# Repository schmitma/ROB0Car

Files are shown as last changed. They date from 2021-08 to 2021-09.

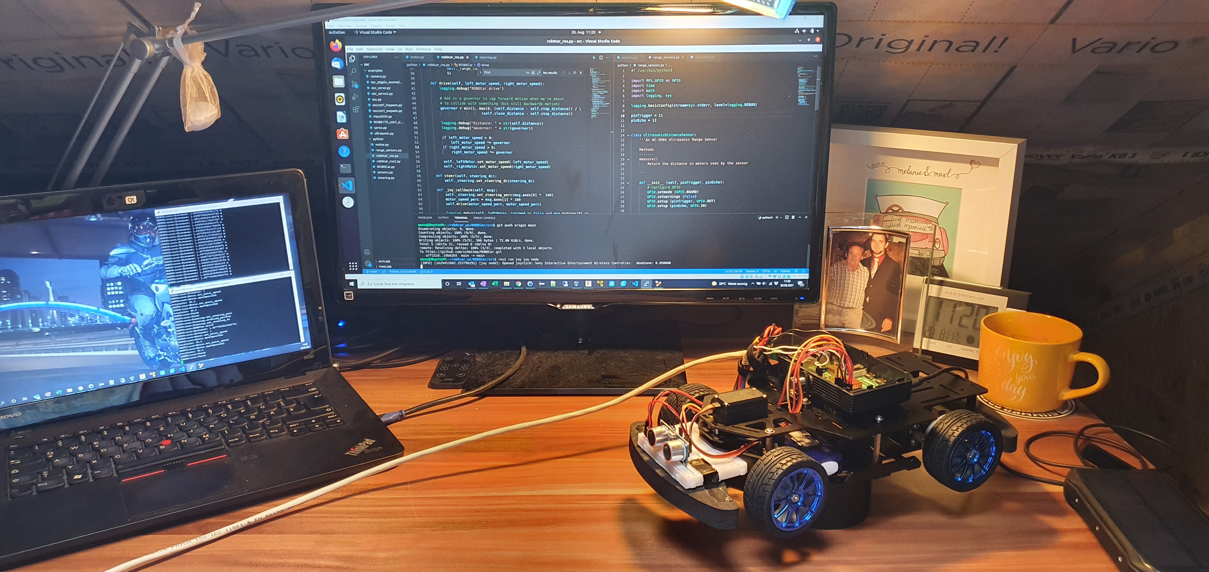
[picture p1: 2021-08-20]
doc/img/20210820_112039.jpg

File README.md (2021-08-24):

# ROB0Car
Build and control an AI-enabled autonomous robot car using the Raspberry Pi, ROS, Python and C/C++

Core-technologies to be used:
 - Raspberry Pi
 - Ubuntu
 - ROS2
 - Python
 - C/C++
 - Visual Studio Code as Editor/IDE
 - SCM using git
 - CAD using Fusion 360
 - 3D-printing using Creality Ender 3 Pro
 - Using AI methods such as neuronal networks

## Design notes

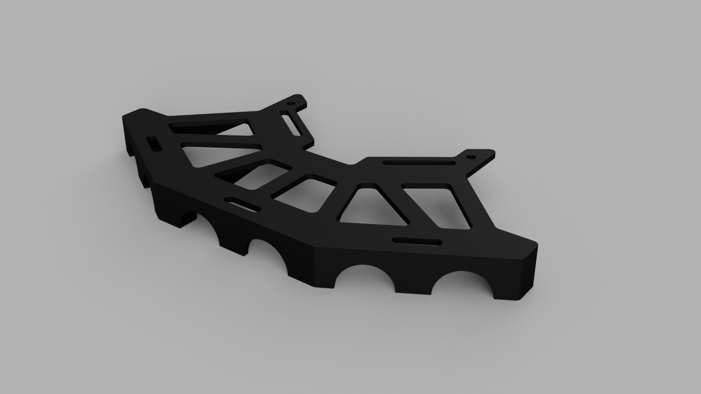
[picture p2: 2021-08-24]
cad/renderings/Front_Mount_HC-SR04.png

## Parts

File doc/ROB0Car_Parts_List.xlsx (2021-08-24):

Picture | Manufacturer | Description | Manufacturer Article Number | EAN | Status | (Estimated) Delivery Date | Stock | Source of supply | Comment | Unit Price incl. VAT [€] | Quantity | Unit | Total Price incl. VAT [€]
 | LABISTS | LABISTS Raspberry Pi 4 Model B 4 GB Ultimatives Kit mit 32GB Class10 Micro SD-Karte, 5,1V 3,0A USB-C EIN/Aus-Schaltnetzteil, 3 Premium Kupfer Kühlkörper, Micro HDMI-Kabel, Premium Schwarzes Gehäuse | B09B9M7TPP |  | In Stock |  | 1.00 | https://www.amazon.de/Raspberry-Ultimatives-Aus-Schaltnetzteil-HDMI-Kabel-K%C3%BChlk%C3%B6rper/dp/B09B9M7TPP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 |  | 87.99 € | 1.00 | pc | 87.99 €
 | WayinTop | WayinTop Ultimate Starter Kit für Raspberry Pi 4 B 3 B+, Ausführliche E-Book Anleitung, Python C Java, 300 Elemente, Elektronische Kit für Raspberry Pi zum Lernen Elektronik und Programmierung |  |  | In Stock |  | 1.00 | https://www.amazon.de/gp/product/B08DQYLLNZ/ref=ppx_yo_dt_b_asin_title_o01_s00?ie=UTF8&psc=1 |  | 34.19 € | 1.00 | pc | 34.19 €
 | LABISTS | LABISTS Ultimate Starter Kit, Raspberry Pi Starter Kit, Support Python C, mit kostenlosen Tutorials, Lötfreies Steckbrett und Zubehör |  |  | In Stock |  | 1.00 |  |  | 44.79 € | 1.00 | pc | 44.79 €
 | DFRobot | DFRobot ROB0170 NXP CUP Race Car Chassis | ROB0170 |  | In Stock |  | 1.00 | https://www.mouser.de/ProductDetail/DFRobot/ROB0170?qs=hWgE7mdIu5TqrtXq%252BmF5EA%3D%3D |  | 86.98 € | 1.00 | pc | 86.98 €
 | DFRobot | DFRobot KIT0166 Brushless DC Motor-Kit for ROB0170 | KIT0166 |  | In Stock |  | 1.00 | https://www.mouser.de/ProductDetail/DFRobot/KIT0166 |  | 38.55 € | 1.00 | pc | 38.55 €
 |  | HC-SR04 Ultraschall-Modul Entfernungssensor für Raspberry Pi, UNO, MEGA2560, Roboter (blau), 5 Stück |  |  | In Stock |  | 2.00 | https://www.amazon.de/gp/product/B081PZF4T3/ref=ppx_yo_dt_b_asin_title_o01_s00?ie=UTF8&psc=1 |  | 7.99 € | 2.00 | pc | 15.98 €
 |  | Schutzmatten 60 x 60cm Schutzmatte Trainingsmatte Puzzlematte Unterlegmatten Poolmatte Fitnessmatten für Bodenschut für Bodenschutz, Büro, Fitnessraum, Bordures |  |  | In Stock |  | 1.00 | https://www.amazon.de/gp/product/B08SQ6NZXJ/ref=ppx_yo_dt_b_asin_title_o06_s00?ie=UTF8&psc=1 | Base for race track | 32.58 € | 1.00 | pc | 32.58 €
 | Arduino | ARDUINO UNO REV 3 |  |  | In Stock |  | 1.00 | https://www.amazon.de/gp/product/B008GRTSV6/ref=ppx_yo_dt_b_asin_title_o03_s00?ie=UTF8&psc=1 |  | 22.00 € | 1.00 | pc | 22.00 €
 | Youmile | Youmile 5 Stücke Geschwindigkeitsmesssensor IR Infrarot Schlitz Optokoppler Modul Lichtschranke Sensor für Motordrehzahlerkennung oder Arduino mit Encoder |  |  | In Stock |  | 1.00 | https://www.amazon.de/gp/product/B0817FM4BJ/ref=ppx_yo_dt_b_asin_title_o05_s01?ie=UTF8&psc=1 |  | 6.99 € | 1.00 | pc | 6.99 €
 | Youmile | Youmile 5 Stücke Geschwindigkeitsmesssensor LM393 Geschwindigkeitsmessmodul Tacho Sensor Slot Typ IR Optokoppler für MCU RPI Arduino DIY Kit mit Encoder |  |  | In Stock |  | 1.00 | https://www.amazon.de/gp/product/B0817H9436/ref=ppx_yo_dt_b_asin_title_o05_s00?ie=UTF8&psc=1 |  | 7.79 € | 1.00 | pc | 7.79 €
 | KINCREA | KINCREA 2.54mm Male Female Dupont Wire Jumper with Pin Header Connector Housing Kit - 620pcs JA001 |  |  | In Stock |  | 1.00 | https://www.amazon.de/gp/product/B07BTB3MC7/ref=ppx_yo_dt_b_asin_title_o02_s00?ie=UTF8&psc=1 |  | 12.99 € | 1.00 | pc | 12.99 €
 | Waveshare | Waveshare 2-DOF Pan-Tilt Hat for Raspberry Pi Zero/Zero W/Zero WH/2B/3B/3B+ Onboard PCA9685 PWM Chip TSL25911FN 16-bit Ambient Light Sensor Make Pi Camera Move and Sense Light Intensity Via I2C |  |  | In Stock |  | 1.00 | https://www.amazon.de/gp/product/B07PPV122Z/ref=ppx_yo_dt_b_asin_title_o01_s00?ie=UTF8&psc=1 |  | 24.99 € | 1.00 | pc | 24.99 €
 | Waveshare | Waveshare MCP23017 IO Expansion Board I2C Interface Expands 16 I/O Pins 8 pcs Stacked and Used at The Same Time Allow Multi I2C Modules to be Stacked |  |  | In Stock |  | 1.00 | https://www.amazon.de/gp/product/B07P2KD39X/ref=ppx_yo_dt_b_asin_title_o00_s00?ie=UTF8&psc=1 |  | 9.75 € | 1.00 | pc | 9.75 €
 | Turnigy | Turnigy E3 Compact 2S/3S Lipo Charger 100-240v (EU Plug) |  |  | In Stock |  | 1.00 | https://hobbyking.com/en_us/turnigy-e3-compact-2s-3s-lipo-charger-100-240v-eu-plug.html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 |  | 13.31 € | 1.00 | pc | 13.31 €
 | Turnigy | Turnigy nano-tech 1500mah 3S 35~70C Lipo Pack |  |  | In Stock |  | 1.00 | https://hobbyking.com/en_us/turnigy-nano-tech-1500mah-3s-35-70c-lipo-pack.html |  | 16.01 € | 1.00 | pc | 16.01 €
 |  | MT60 3 Pole Motor / ESC Connector Set 12AWG Black Male - Female (2 set) |  |  | In Stock |  | 2.00 | https://hobbyking.com/en_us/mt60-3-pole-motor-esc-connector-set-12awg-black-male-female-2-set.html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 |  | 3.05 € | 2.00 | pc | 6.10 €
 |  | Align Motor Pinion Gear 13T T-Rex 450 PRO # H45059 |  |  | In Stock |  | 2.00 | https://www.live-hobby.de/en/Accessories/Drives/Brushless-ESC-Motors/Motor-Pinion-Gear/Align-Motor-Pinion-Gear-13T-T-Rex-450-PRO-H45059.html |  | 3.79 € | 2.00 | pc | 7.58 €
 |  |  |  |  |  |  |  |  |  | Total Price incl. VAT [€] |  |  | 468.57 €

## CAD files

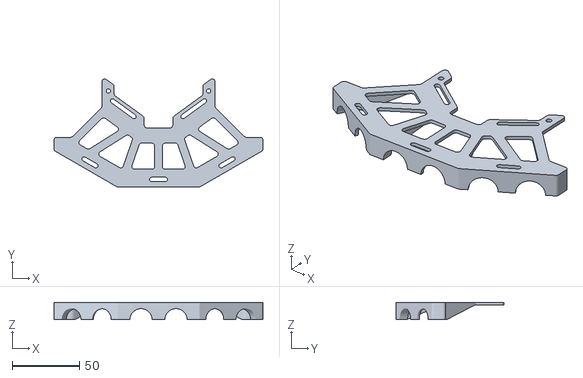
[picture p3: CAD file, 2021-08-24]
cad/Front_Mount_HC-SR04.stl
155.3 x 80.4 x 13.0

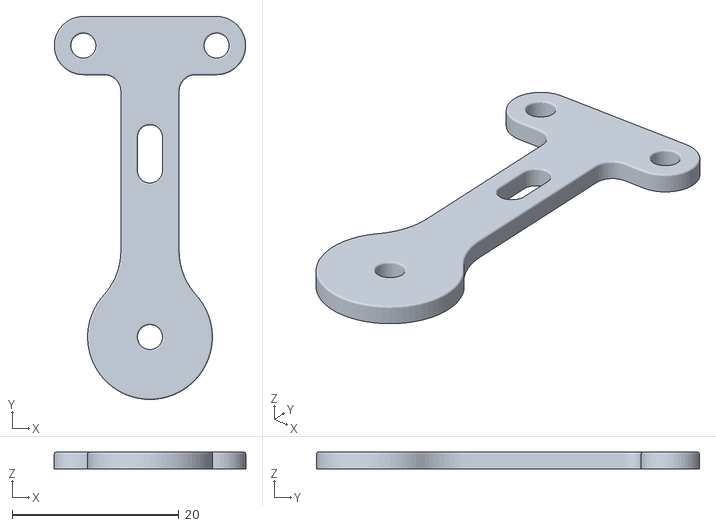
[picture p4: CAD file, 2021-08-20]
cad/Steering_Transmission_Plate.stl
23.0 x 46.0 x 2.00

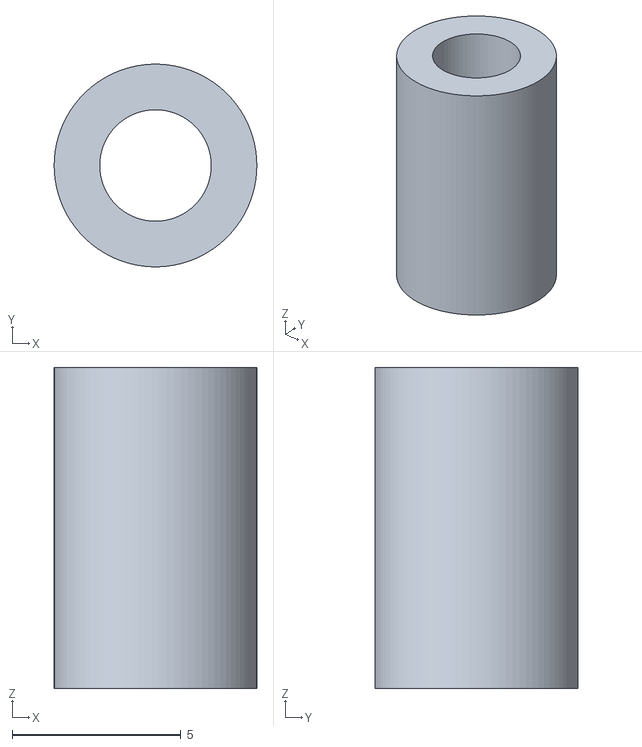
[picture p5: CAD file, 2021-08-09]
cad/3_3x9_5_Plastic_Spacer.stl
6.00 x 6.00 x 9.50

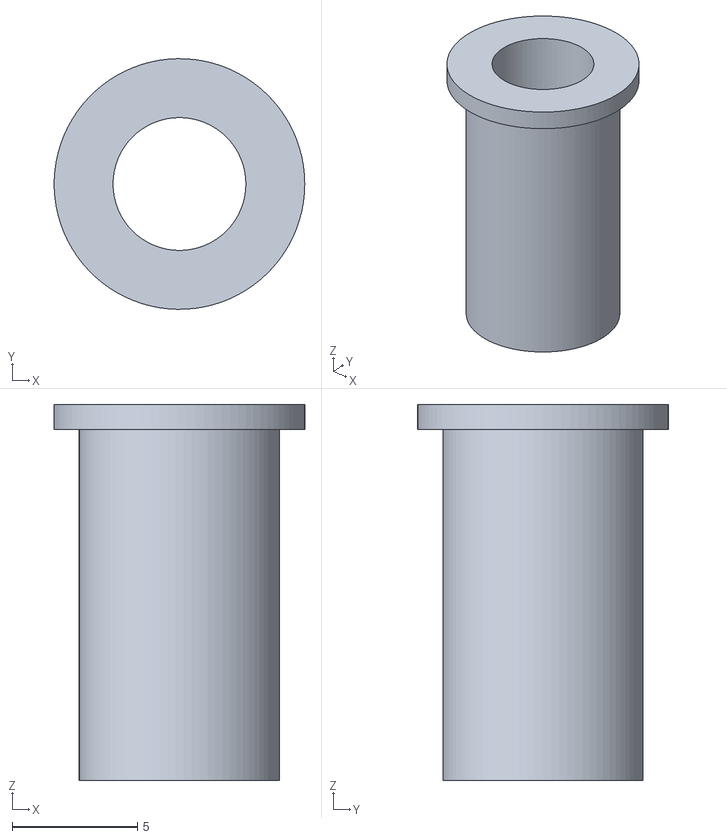
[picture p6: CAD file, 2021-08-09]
cad/5_3x8x15_Plastic_Spacer.stl
10.00 x 10.00 x 15.0

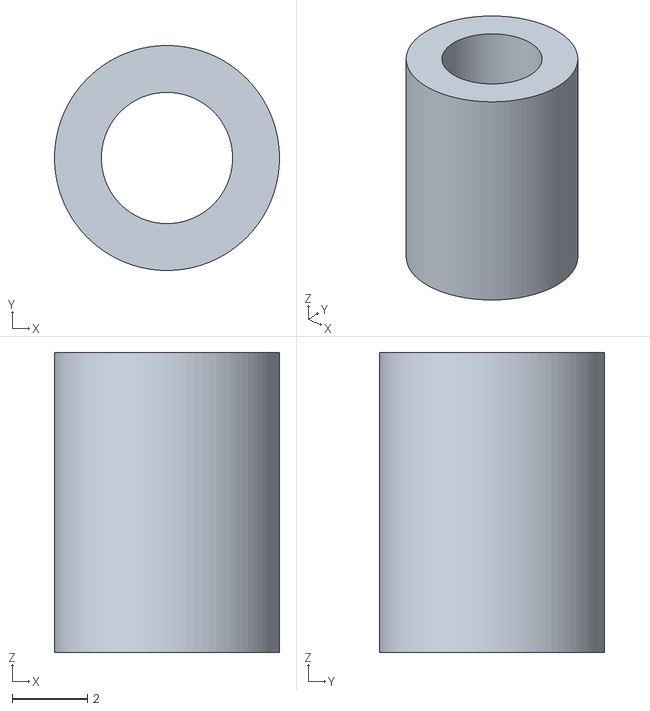
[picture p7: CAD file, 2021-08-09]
cad/3_5x8_Plastic_Spacer.stl
6.00 x 6.00 x 8.00

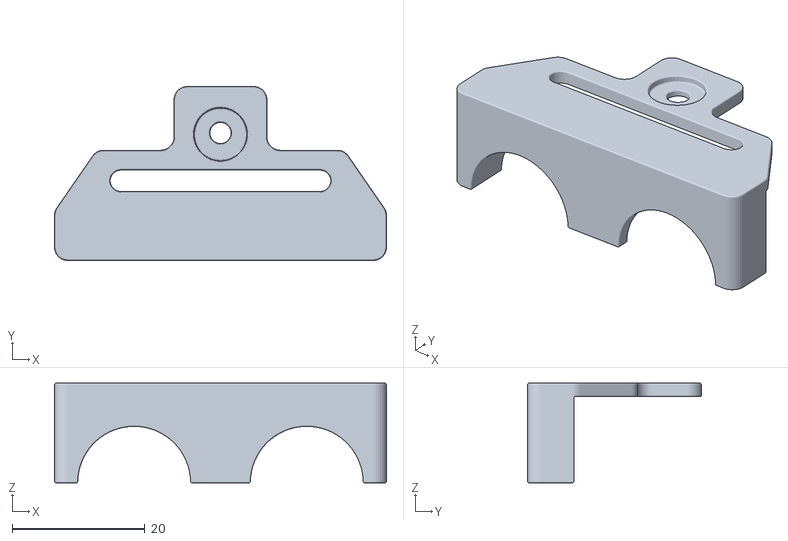
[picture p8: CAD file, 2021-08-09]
cad/Side_Mount_HC-SR04.stl
50.0 x 26.2 x 15.0

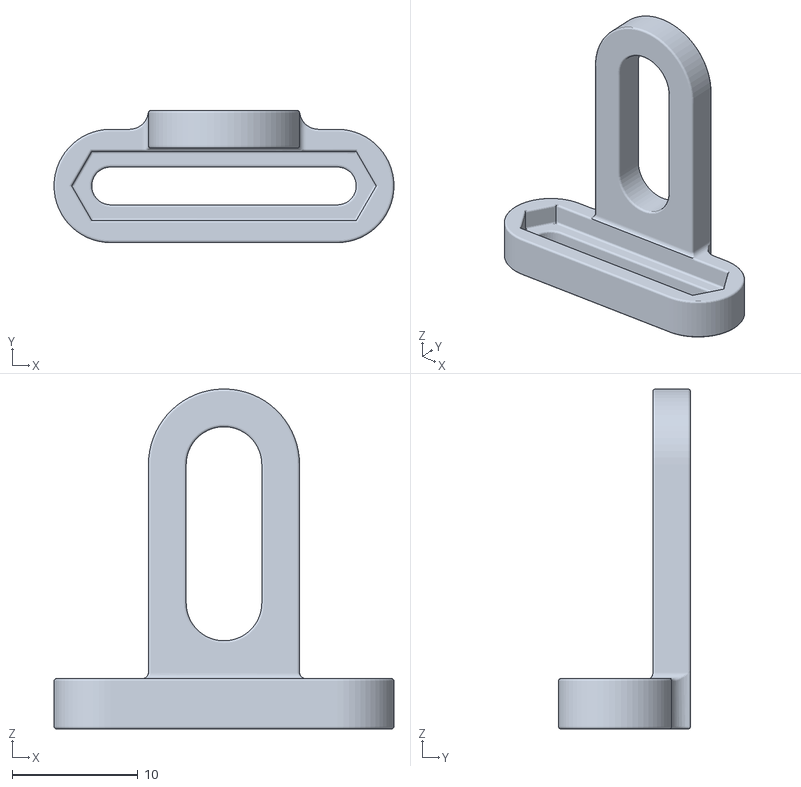
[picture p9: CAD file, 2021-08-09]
cad/Mount_RaspberryPi.stl
27.0 x 10.5 x 27.0

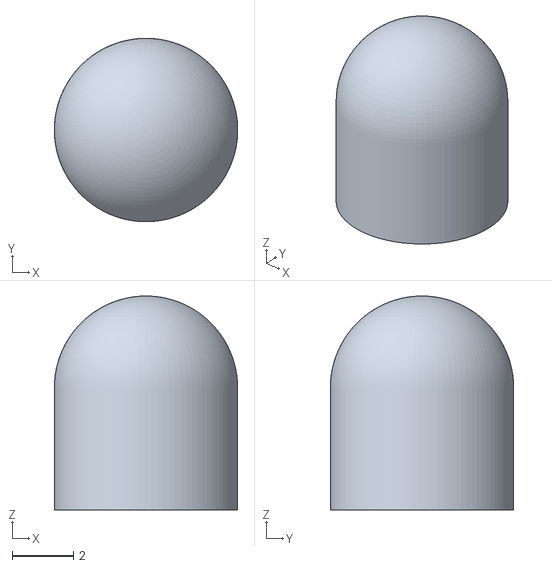
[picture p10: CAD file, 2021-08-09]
cad/3_5x4_Motor_End_Cap.stl
6.00 x 6.00 x 7.00

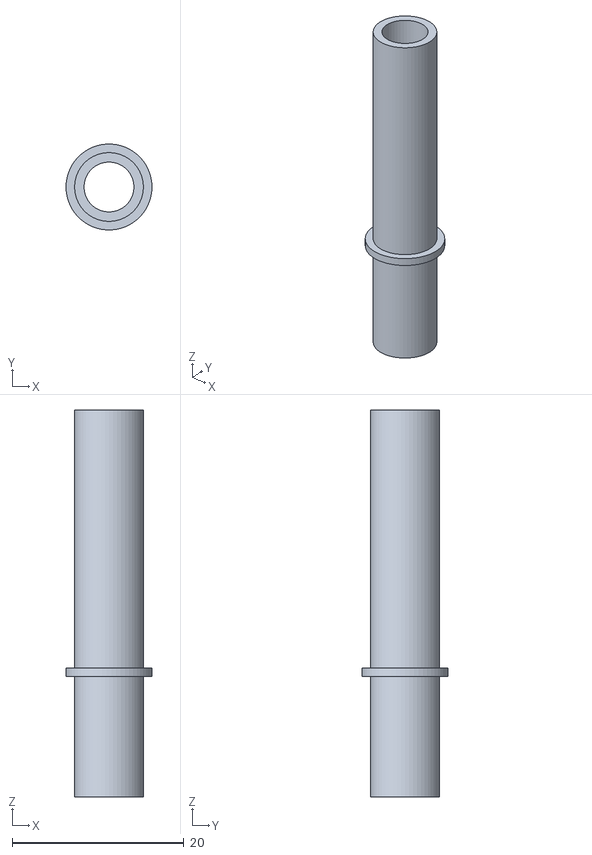
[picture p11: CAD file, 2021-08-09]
cad/5_8x8x45_Plastic_Spacer.stl
10.0 x 9.99 x 45.0

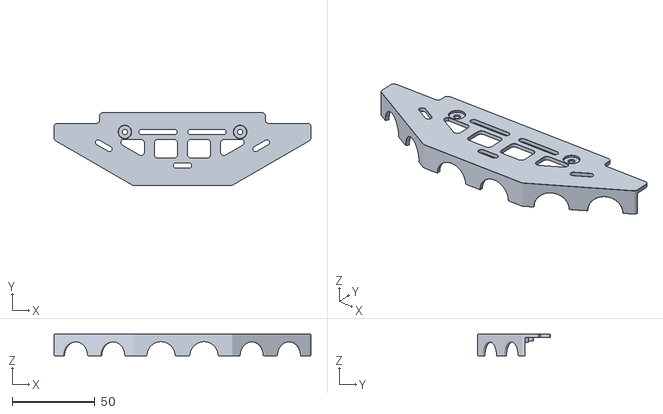
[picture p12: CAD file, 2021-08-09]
cad/Back_Mount_HC-SR04.stl
155.3 x 44.0 x 13.0

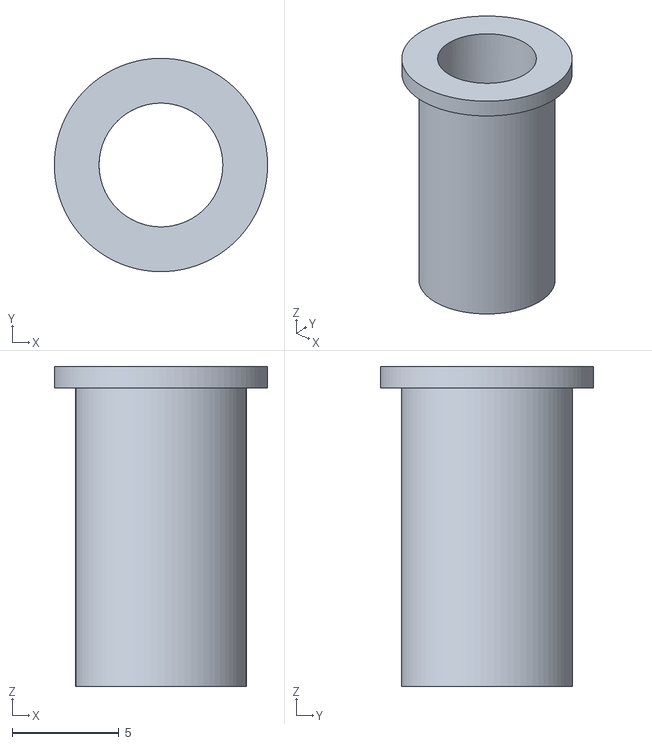
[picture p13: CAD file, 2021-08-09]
cad/5_8x8x15_Plastic_Spacer.stl
10.00 x 10.00 x 15.0

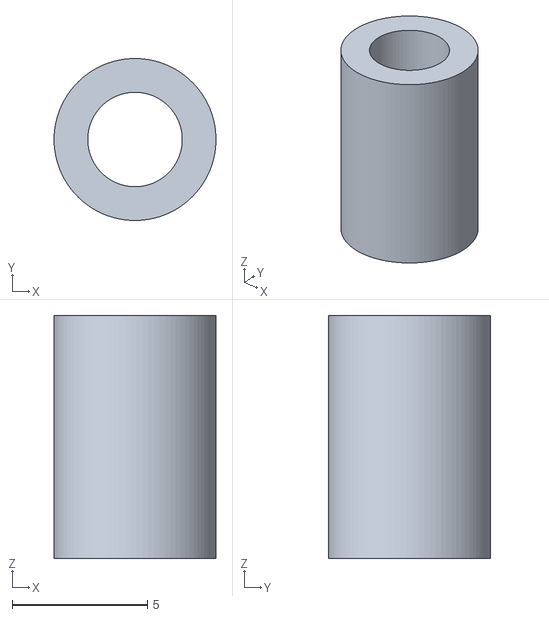
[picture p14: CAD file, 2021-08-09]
cad/3_5x9_Plastic_Spacer.stl
6.00 x 6.00 x 9.00

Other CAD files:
cad/3_6x9_5_Plastic_Spacer.stl

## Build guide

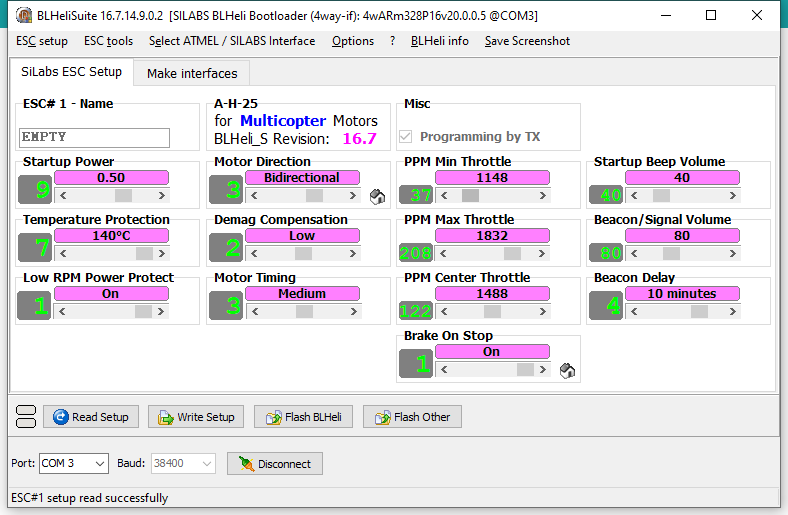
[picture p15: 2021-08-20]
doc/BLHeliSuiteSiLabs_ESC_Setup.png

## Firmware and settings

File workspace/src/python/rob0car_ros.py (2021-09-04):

#! /usr/bin/env python3
import pigpio
import os
import logging
import sys
import rclpy
from rclpy.node import Node
from sensor_msgs.msg import Joy, Range
from motor import Motor
from steering import Steering
from camera import Camera


logging.basicConfig(stream=sys.stderr, level=logging.DEBUG)

class ROB0Car(Node):
    def __init__ (self):
        logging.debug("ROBOCar.__init__")

        super().__init__('ROB0Car')

        self._leftMotor = Motor(13, 'PWM')
        self._rightMotor = Motor(5, 'PWM', True)
        self._steering = Steering(23)

        self._camera = Camera()

        self.close_distance = 0.30 # start slowing down when obstacle within 30 cm is detected
        self.stop_distance = 0.10 # stop motion in direction where obstacle within 10 cm has been detected
        self.distance = 400.0

        self._joy_subscription = self.create_subscription(
            Joy,
            'joy',
            self._joy_callback,
            5)

        self._range_subscription = self.create_subscription(
            Range,
            'range',
            self._range_callback,
            5)

    def drive(self, left_motor_speed, right_motor_speed):
        logging.debug("ROBOCar.drive")

        # Add in a governor to cap forward motion when we're about
        # to collide with something (but still backwards motion)
        governor = min(1, max(0, (self.distance - self.stop_distance)) / \
                           (self.close_distance - self.stop_distance))
        
        logging.debug("Distance: " + str(self.distance))
        logging.debug("Governor: " + str(governor))

        if left_motor_speed > 0:
            left_motor_speed *= governor
        if right_motor_speed > 0:
            right_motor_speed *= governor
        
        self._leftMotor.set_motor_speed(left_motor_speed)
        self._rightMotor.set_motor_speed(right_motor_speed)

    def steer(self, steering_dc):
        self._steering.set_steering_dc(steering_dc)

    def _joy_callback(self, msg):
        logging.debug(f'Joystick axes: {msg.axes}')
        logging.debug(f'Joystick buttons: {msg.buttons}')
        self._steering.set_steering_perc(msg.axes[0] * -100)
        motor_speed_perc = msg.axes[1] * 100
        self.drive(motor_speed_perc, motor_speed_perc)

        logging.debug(self._leftMotor._isArmed == False and msg.buttons[0] == 1)
        logging.debug(self._rightMotor._isArmed == False and msg.buttons[0] == 1)
        
        if self._leftMotor._isArmed == False and msg.buttons[0] == 1:
            self._leftMotor.arm()

        if self._rightMotor._isArmed == False and msg.buttons[0] == 1:
            self._rightMotor.arm()

        if msg.buttons[1] == 1:
            self._camera.home()
        
        if msg.axes[3] != 0:
            self._camera.pan(self._camera.pan_angle + msg.axes[3])
        if msg.axes[4] != 0:
            self._camera.tilt(self._camera.tilt_angle + (msg.axes[4] * (-1)))

    def _range_callback(self, msg):
        self.distance = msg.range
        
def main(args=None):
    logging.debug("main")
    # initialize the rob0car node
    rclpy.init(args=args)
    rob0car = ROB0Car()

    # wait for incoming commands
    logging.debug("main: Waiting for incoming ROS2 messages on topic joy.")
    rclpy.spin(rob0car)

    # Interrupt detected, shut down
    #rob0car.stop()
    rob0car.destroy_node()
    rclpy.shutdown()

if __name__ == '__main__':
    main()

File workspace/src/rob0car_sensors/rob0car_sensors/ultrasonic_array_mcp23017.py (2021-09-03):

#!/usr/bin/env python3

import time
import pigpio # https://abyz.me.uk/rpi/pigpio/python.html
import sys
import logging
import re
import queue
import argparse

logging.basicConfig(stream=sys.stderr, level=logging.DEBUG)

# Resources:
# - MCP23017 datasheet: https://ww1.microchip.com/downloads/en/devicedoc/20001952c.pdf

# TODO:
# - Use Banking mode -> implement Dictionary to switch between register address mapping
# - Use interrupts
# - Improve performance using parallelism -> check if parallelism improves speed since steps have to be carried out sequentially?
# - Apply coding guidelines, e.g. PEP8

# General process for interrupt driven operation
# 1. Trigger all sensors by setting all bits of GPIOA register to high
# 2. If interrupt occurs determine sensors for which echo signal has changed
#    by comparing old and new state of GPIOB register
# 3. If rising edge has been detected save start time
# 4. If falling edge has been detected save stop time and calculate distance

MCP23017_I2C_ADDR = 0x27

# According to the MCP23017 datasheet:
# The 16-bit I/O port functionally consists of two 8-bit ports (PORTA and 
# PORTB).  The MCP23X17 can be configured to operate in the 8-bit or 16-bit 
# modes via IOCON.BANK.
#
# The BANK bit changes how the registers are mapped:
# If BANK = 1, the registers associated with each port are segregated.
# Registers associated with PORTA are mapped from address 00h - 0Ah and
# registers associated with PORTB are mapped from 10h - 1Ah.
# If BANK = 0, the A/B registers are paired.  For example, IODIRA is mapped
# to address 00h and IODIRB is mapped to the next address (address 01h). 
# The mapping for all registers is from 00h -15h.
#
# To take this into account the register mapping is implemented as a
# dictionary, using the register name as key. The corresponding value is a
# list containing the register address for 8-bit mode at index 0 and 
# containing the register address for 16-bit mode (banked-mode) at
# index 1.
MCP23017_REGISTER_MAPPING = {
    "IODIRA":   [0x00, 0x00], 
    "IODIRB":   [0x01, 0x10],
    "IPOLA":    [0x02, 0x01],
    "IPOLB":    [0x03, 0x11],
    "GPINTENA": [0x04, 0x02],
    "GPINTENB": [0x05, 0x12],
    "DEFVALA":  [0x06, 0x03],
    "DEFVALB":  [0x07, 0x13],
    "INTCONA":  [0x08, 0x04],
    "INTCONB":  [0x09, 0x14],
    "IOCON1":   [0x0A, 0x05],
    "IOCON2":   [0x0B, 0x15],
    "GPPUA":    [0x0C, 0x06],
    "GPPUB":    [0x0D, 0x16],
    "INTFA":    [0x0E, 0x07],
    "INTFB":    [0x0F, 0x17],
    "INTCAPA":  [0x10, 0x08],
    "INTCAPB":  [0x11, 0x18],
    "GPIOA":    [0x12, 0x09],
    "GPIOB":    [0x13, 0x19],
    "OLATA":    [0x14, 0x0A],
    "OLATB":    [0x15, 0x1A]
}

# MCP23017 configuration register flags (IOCON ADDR 0x05)
IOCON_INTPOL = (1<<1)
IOCON_SEQOP  = (0<<5)
IOCON_MIRROR = (0<<6)
IOCON_BANK   = (1<<7)

MODE = (IOCON_INTPOL + 
        IOCON_SEQOP + 
        IOCON_MIRROR + 
        IOCON_BANK)

SENSORS = (("FRONT_RIGHT", 0),
           ("FRONT_MIDDLE", 1),
           ("FRONT_LEFT", 2),
           ("LEFT", 3),
           ("REAR_LEFT", 4),
           ("REAR_MIDDLE", 5),
           ("REAR_RIGHT", 6),
           ("RIGHT", 7))

class HCSR04:
    def __init__(self, pos, gpio):
        # Maybe define position in coordinates?
        # x, y, z from center + angular orientation?
        self.position = pos
        self.gpio_assignment = gpio
        self.distance_cm = 0

class HCSR04Cluster:

    """
    Class to read up to 8 HC-SR04 ultrasonic sensors attached
    to a MCP23017 I2C port expander.

    Each sensor needs two GPIOs, one for the echo pin and one for
    the trigger pin.

    The MCP23017 has a total of 16 GPIOs: 8 on bank A and 8 on bank B

    Bank A is configured as output and should be connected
    to the sensor echo pins.  Bank B is configured as input
    and should be connected to the sensor trigger pins.

    The sensors are referred to as sensor 0 to sensor 7. Sensor x
    should be connected to pin Ax (trigger) and pin Bx (echo).

    Two modes of operation are supported - interrupt driven or not
    interrupt driven.  The interrupt driven mode is preferred but
    requires the use of one spare Pi GPIO. This GPIO should be
    connected to pin 20 (INTA) of the MCP23017.

    The range is reported in cms.  An invalid reading is
    reported as 9999.
    """
    # To get fast sequential banked mode is used. If banked
    # mode isn't used then only half the accuracy will be achieved.

    MCP23017_I2C_ADDR = 0x27
       
    IODIRA=0x00
    IODIRB=0x01

    IOCONA=0x0A
    IOCONB=0x0B

    GPIOA=0x12
    GPIOB=0x13

    GPINTENA=0x02
    DEFVALA=0x03
    INTCONA=0x04
    
    # Value of TRIGGER_GAP has to be changed if interrupt-driven
    # mode is used and sensor values are incorrect.

    TRIGGER_GAP=430 # Microseconds between trigger and echo going high.

    SPEED_OF_SOUND = 340.29 # metres per second

    MICS2CMS = SPEED_OF_SOUND / 20000.0 # Allowing for round trip

    INVALID_READING=9999.0

    def __init__(self,
                 i2c_addr = MCP23017_I2C_ADDR, 
                 i2c_channel = 1, 
                 # Interrupt based operation is enabled if a GPIO to process
                 # the interrupt signal is supplied.
                 INTB_GPIO = None,
                 mode = MODE,
                 sensor_configuration = 0xFF,
                 i2c_kbps = 100.0, 
                 max_range_cm = 450):
        """
        Instantiate with the Pi and the I2C address of the
        MCP23017.

        Optionally the I2C bus may be specified (default: 1).

        Optionally the GPIO connected to the interrupt line
        of the MCP23017 may be specified (default: None).

        Optionally the I2C bus speed may be specified (default
        100 kbps). This parameter should be specified if a different
        then standard I2C bus speed is used.

        Optionally the sensors maximum range in centimetres may
        be specified (default: 450).
        """
        self.pi=pigpio.pi() # Connect to local Pi.

        if not self.pi.connected:
            exit(0)

        self._cb = None
        self._INTB_GPIO = INTB_GPIO
        self._MODE = mode
        self._BANKING_MODE_IS_ACTIVE = 1 if (self._MODE | IOCON_BANK) else 0
        self._sensor_configuration = sensor_configuration

        sensor_config_idzs = [m.start() for m in re.finditer("1", '{0:08b}'.format(self._sensor_configuration)[::-1])]
        self.sensors = [HCSR04(SENSORS[s][0], SENSORS[s][1]) for s in sensor_config_idzs]
        
        self.number_of_sensors = len(self.sensors)
        self.sensor_bitmask = sum([1 << x.gpio_assignment for x in self.sensors])

        self._timeout = (2.0 * max_range_cm / 100.0) / HCSR04Cluster.SPEED_OF_SOUND

        if self._timeout < 0.001:
            self._timeout = 0.001
        elif self._timeout > 0.05:
            self._timeout = 0.05
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

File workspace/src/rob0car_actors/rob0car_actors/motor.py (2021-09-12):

#! /usr/bin/env python3
import pigpio
import os
import logging
import sys
import time
import numpy as np

logging.basicConfig(stream=sys.stderr, level=logging.DEBUG)

# ESC Protocol settings
min_throttle_default_us = 1000
max_throttle_default_us = 2000
center_throttle_default_us = 1500

frequency_Hz = {
    'PWM': 200,          # max. frequency: 500 Hz
    'Oneshot125': 1000,  # max. frequency: 4 kHz
    'Oneshot42': 4000,   # max. frequency: 12 kHz
    'Multishot': 8000    # max. frequency: 32 kHz
}

divider = {
    'PWM': 1,
    'Oneshot125': 8,
    'Oneshot42': 24,
    'Multishot': 80
}

class Motor:
    '''A brushless DC motor driven by one pin on a Raspberry Pi.'''

    def __init__ (self, pin, protocol='PWM', isInverted=False):
        logging.debug("Motor.__init__")
        #  Configure GPIO
        if os.system ("pgrep pigpiod") != 0:
            logging.debug("Starting pipgiod")
            os.system("sudo pigpiod")

        self._pi = pigpio.pi()  # Connect to PIGPIO-Daemon
        self._pin = pin
        self._protocol = protocol

        # pigpio.set_PWM_frequency(): Returns the numerically closest frequency if OK, 
        # otherwise PI_BAD_USER_GPIO or PI_NOT_PERMITTED.
        self._frequency = self._pi.set_PWM_frequency(pin, frequency_Hz.get(self._protocol, 200))
        if self._frequency == pigpio.PI_BAD_USER_GPIO or self._frequency == pigpio.PI_NOT_PERMITTED:
            sys.exit('No valid frequency!')

        self._speed = 0
        self._max_speed_perc = 20
        self._isArmed = False
        self._isInverted = isInverted
        self._min_throttle_us = min_throttle_default_us / divider.get(self._protocol, 1)
        self._max_throttle_us = max_throttle_default_us / divider.get(self._protocol, 1)
        self._center_throttle_us = center_throttle_default_us / divider.get(self._protocol, 1)
        self._period_length_us = ((1/self._frequency) * (10 **6))
        self._min_dc = self._min_throttle_us / self._period_length_us * 100
        self._max_dc = self._max_throttle_us / self._period_length_us * 100
        self._center_dc = self._center_throttle_us / self._period_length_us * 100

        self._pi.set_mode(pin, pigpio.OUTPUT)
        self._pi.set_PWM_range(pin, 100)  # Control PWM from 0 .. 100 %
        self._pi.set_PWM_dutycycle(self._pin, 0)

    def speedperc2dc(self, mot_speed_perc):
        logging.debug("Motor.speedperc2dc")
        slope = (self._max_dc-self._center_dc)/100
        mot_speed_lim_perc = min(self._max_speed_perc, abs(mot_speed_perc)) * np.sign(mot_speed_perc)
        dc = self._center_dc + mot_speed_lim_perc * slope
        dc_lim = min(max(dc, self._min_dc), self._max_dc)
        print('DutyCycle: ' + str(dc))
        return dc_lim

    def arm(self):
        logging.debug("Motor.arm")
        max_arming_throttle_dc = 7.5
        arming_throttle_dc_step = 0.1
        arming_throttle_dc_wait = 0.1

        self._pi.set_PWM_dutycycle(self._pin, 0)
        time.sleep(1)

        self._pi.set_PWM_dutycycle(self._pin, self.speedperc2dc(80))
        time.sleep(1)
        self._pi.set_PWM_dutycycle(self._pin, self.speedperc2dc(30))
        time.sleep(1)

        self._isArmed = True

    def set_motor_speed(self, speed):
        logging.debug("Motor.set_motor_speed")
        if not self._isArmed:
            return
        if self._isInverted:
            speed *= -1    
        self._pi.set_PWM_dutycycle(self._pin, self.speedperc2dc(speed))
        self._speed = speed

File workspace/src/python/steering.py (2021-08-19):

#!/usr/bin/python3
import os
import pigpio
import logging
import sys

logging.basicConfig(stream=sys.stderr, level=logging.DEBUG)

# Empirically determined center position of steering
steering_center_pos_us = 1570
# Empirically determined offset in us for max. steering angle
steering_offset_us = 175

class Steering:
    '''A servo motor driven by one pin on a Raspberry Pi.'''

    def __init__ (self, pin):
        logging.debug("Steering.__init__")
        #  Configure GPIO
        if os.system ("pgrep pigpiod") != 0:
            os.system("sudo pigpiod")

        self._pi = pigpio.pi()  # Connect to PIGPIO-Daemon
        self._pin = pin

        self._pi.set_mode(pin, pigpio.OUTPUT)
        self._pi.set_servo_pulsewidth(self._pin, 0)

    def set_steering_dc(self, steering_dc):
        logging.debug("Steering.set_steering_dc")
        self._pi.set_servo_pulsewidth(self._pin, steering_dc)

    def set_steering_perc(self, steering_perc):
        logging.debug("Steering.set_steering_perc")
        self.set_steering_dc(self.steering_perc2dc(steering_perc))

    def steering_perc2dc(self, steering_perc):
        logging.debug("Steering.steering_perc2dc")
        slope = steering_offset_us / 100
        return steering_perc * slope + steering_center_pos_us

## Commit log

2021-08-09 Transfered current working state for project ROB0Car from local directory to git-repo.
    [3_3x9_5_Plastic_Spacer.stl, 3_5x4_Motor_End_Cap.stl, 3_5x8_Plastic_Spacer.stl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]
2021-08-13 Fixed number of arguments for function speedperc2dc in motor.py.
    [motor.py]
2021-08-13 Fixed return value of function speedperc2dc in motor.py.
    [motor.py]
2021-08-13 Added class Steering.
2021-08-13 Fixed bug in steering.py.
    [steering.py]
2021-08-16 Added debug output in motor.py.
2021-08-16 Imported sys to fix dependency in motor.py.
    [motor.py]
2021-08-16 Bugfix indentations in rob0car_ros.py.
    [rob0car_ros.py]
2021-08-16 Fixed typos in rob0car_ros.py.
    [rob0car_ros.py]
2021-08-16 Imported sys in steering.py to fix dependency issue.
    [steering.py]
2021-08-16 Added possibility to control motors via joystick in rob0car_ros.py.
2021-08-16 Added arming sequence to motor.py.
2021-08-16 Fixed and operator bug in motor.py.
    [rob0car_ros.py]
2021-08-16 Changed comparison in motor.py.
2021-08-16 Adapted if statement conditions in motor.py.
2021-08-16 Fixed function call to Motor.arm() in rob0car_ros.py.
    [rob0car_ros.py]
2021-08-16 Adapted arming sequence for BLHeli_S in motor.py.
2021-08-16 Exchanged range for np.arange in motor.py.
2021-08-17 Added Datasheet for Ultrasonic Ranging Module HC-SR04.
2021-08-17 Updated ultrasonic.py
2021-08-17 Added functionality for ultrasonic range sensor.
2021-08-18 Adapted arming sequence in motor.py.
2021-08-18 Bugfix of dc calculation in motor.py.
    [motor.py]
2021-08-19 Extended motor.py with further ESC protocols.
2021-08-19 Bugfix of dictionary acces in motor.py.
    [motor.py]
2021-08-19 Bugfix in governor calculation and correction of left motor driving direction in rob0car_ros.py
    [motor.py, rob0car_ros.py]
2021-08-19 Added correction values for center position and max. steering angles in steering.py
    [steering.py]
2021-08-20 Added flag for motor direction inversion in motor.py.
2021-08-20 Added various datasheets to doc.
    [Steering_Transmission_Plate.stl]
2021-08-20 Added image of first prototype to doc/img.
2021-08-20 Corrected steering direction to match joystick in rob0car_ros.py.
    [rob0car_ros.py]
2021-08-20 Bugfix: Corrected motor speed limitation to work in both directions in motor.py.
    [motor.py]
2021-08-22 Added ultrasonic_pcf8574.py to examples.
2021-08-22 Fixed indentation error in ultrasonic_pcf8574.py.
    [ultrasonic_pcf8574.py]
2021-08-23 Extended example ultrasonic_pcf8574.py.
2021-08-23 Bugfix I2C functions in example ultrasonic_pcf8574.py.
    [ultrasonic_pcf8574.py]
2021-08-23 Added ROB0Car_Parts_List.xlsx.
    [ROB0Car_Parts_List.xlsx]
2021-08-24 Revised Front_Mount_HC-SR04.
    [Front_Mount_HC-SR04.stl]
2021-08-25 Added ultrasonic_mcp23017.py to examples.
2021-08-25 Bugfix in ultrasonic_mcp23017.py.
2021-08-25 Extended debugging output in ultrasonic_mcp23017.py.
2021-08-25 Added ultrasonic_array_mcp23017.py to examples.
2021-08-25 Multiple bugfixes in ultrasonic_array_mcp23017.py.
    [ultrasonic_array_mcp23017.py]
2021-08-25 Added i2c_sonar.py to examples.
2021-08-25 Fixed register addresses in i2c_sonar.py.
    [i2c_sonar.py]
2021-08-25 Reset i2c_sonar.py to example from http://abyz.me.uk/rpi/pigpio/code/i2c_sonar_py.zip.
    [i2c_sonar.py]
2021-08-25 Added debug outputs to i2c_sonar.py.
2021-08-25 Adapted ultrasonic_array_mcp23017.py.
2021-08-26 Refactored ultrasonic_array_mcp23017.py.
2021-08-26 Various bugfixes in ultrasonic_array_mcp23017.py.
    [ultrasonic_array_mcp23017.py]
2021-08-26 Prepared ultrasonic_array_mcp23017.py for interrupt based operation.
2021-08-27 Implemented functions for interrupt driven operation in ultrasonic_array_mcp23017.py.
2021-08-28 Added debug outputs to ultrasonic_array_mcp23017.py.
2021-08-29 Bugfix register configuration in ultrasonic_array_mcp23017.py.
    [ultrasonic_array_mcp23017.py]
2021-08-29 Optimized register configuration in ultrasonic_array_mcp23017.py.
2021-08-29 Bugfix for bitwise operation in ultrasonic_array_mcp23017.py.
    [ultrasonic_array_mcp23017.py]
2021-08-29 Adapted register settings in ultrasonic_array_mcp23017.py.
2021-08-29 Adapted interrupt logic in ultrasonic_array_mcp23017.py.
2021-08-29 Added debugging output to ultrasonic_array_mcp23017.py.
2021-08-29 Bugfix in interrupt logic in ultrasonic_array_mcp23017.py.
    [ultrasonic_array_mcp23017.py]
2021-08-29 Changed sensor configuration in ultrasonic_array_mcp23017.py.
2021-08-30 Activated timeout for distance measurement in ultrasonic_array_mcp23017.py.
2021-08-30 Activated timeout for distance measurement in interrupt driven operation in ultrasonic_array_mcp23017.py.
2021-08-30 Added debug output to ultrasonic_array_mcp23017.py.
2021-08-30 Bugfix string processing in ultrasonic_array_mcp23017.py.
    [ultrasonic_array_mcp23017.py]
2021-08-30 Bugfix control flow in ultrasonic_array_mcp23017.py.
    [ultrasonic_array_mcp23017.py]
2021-08-30 Implemented exception handling for interrupt driven operation in ultrasonic_array_mcp23017.py.
2021-08-31 Added argument parser for command line interface in ultrasonic_array_mcp23017.py.
2021-08-31 Extended command line interface in ultrasonic_array_mcp23017.py.
2021-08-31 Bugfix indexing error in ultrasonic_array_mcp23017.py.
    [ultrasonic_array_mcp23017.py]
2021-09-03 Added examples for Raspberry Pi Pan/Tilt Hat.
2021-09-03 Bugfix - corrected shebang in pca9685.py and rpi_pan_tilt_hat_example.py.
    [pca9685.py, rpi_pan_tilt_hat_example.py]
2021-09-04 Bugfixes in servo control in rpi_pan_tilt_hat_example.py.
    [rpi_pan_tilt_hat_example.py]
2021-09-04 Adapted pin assignments in rob0car_ros.py.
2021-09-04 Added module camera.py.
2021-09-04 Extended camera functionality in rob0car_ros.py.
2021-09-04 Replaced smbus by pigpio in pca9685.py due to permission problems.
    [pca9685.py]
2021-09-04 Bugfix in i2c logic in pca9685.py.
    [pca9685.py]
2021-09-04 Bugfix in camera.py.
2021-09-04 Bugfix axes indizes in rob0car_ros.py.
    [rob0car_ros.py]
2021-09-04 Bugfix tilt direction control with joystick in rob0car_ros.py.
    [rob0car_ros.py]
2021-09-14 Bugfix dependencies in ros2 package rob0car_actors.
    [camera_pan_tilt.py]
2021-09-16 Bugfix of dependencies in rob0car_sensors.py.
    [rob0car_sensors.py]
